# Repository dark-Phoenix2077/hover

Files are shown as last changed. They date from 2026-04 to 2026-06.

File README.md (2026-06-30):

# Hover
A fully custom mini racing/stunt drone with ML-assisted balancing, automatic stunts, and some level of autonomous operation without costly cameras or GPS.

Screenshot 2026-04-16 at 4 11 55 pm

## Why I built this

I wanted a challenge that forced me to learn PCB design and embedded firmware from 
scratch, but also let me apply the area I already know well - machine learning. Designing
a drone from a blank schematic, writing every driver by hand, and then training a custom 
tiny ML model felt like the right way to do all of that at once. My goal was simply to push my first ever hardware project as far as I could, not to have a completely polished project.

## What the project is

Hover is a tiny brushed micro quadcopter built entirely from custom hardware and
firmware. There is no off-the-shelf flight controller, no commercial RC receiver, and no
pre-written driver code. Everything was written/designed from scratch by me.

The system has two PCBs:

Flight Controller (FC): A 4-layer X-shaped PCB with a motor in each corner. It runs an
STM32F103C8T6 at 72MHz, an ICM-42688-P IMU over SPI, a BK2423 2.4GHz RF transceiver, 
and four brushed motor drive circuits.

Screenshot 2026-04-16 at 4 12 30 pm

Remote Control (RC): A 2-layer PCB inside a 3D-printed enclosure. It uses
the same STM32F103C8T6 and BK2423 RF ICs. It has two analog joysticks (ADC + DMA) for
throttle, yaw, pitch, and roll, and eight buttons which are used for arming, auto take-off, auto land,
return-to-home, a 360-degree flip trigger (one of my goals for this was to have some kind of smart one-button trick, and for this goal I settled on the 360 flip), and three spares for future use.

Screenshot 2026-04-16 at 4 14 29 pm

apart from that, this repository also includes:

ML Pipeline: A training and conversion pipeline for an onboard stabilisation model.
Training data will be collected from real flight telemetry once the hardware is
bought. The model will be converted to TFLite and dropped directly into the
FC firmware, which already has the inference code in place and waiting.

CAD: Both the drone body and RC enclosure were designed in Onshape. The drone frame
is a minimal 2-shell design with motor mounts, battery tray, and canopy, with both shells 
sandwiching the PCB in the middle. The RC enclosure uses the same 2-shell design with joystick 
cutouts, button extenders, and a battery bay below the PCB.

Screenshot 2026-04-16 at 4 15 18 pm

Screenshot 2026-04-16 at 4 16 22 pm

Firmware: Firmware created for both the FC and RC in STM32 CubeMX and CubeIDE, all firmware should work but is untested as I do not have the hardware right now. additionally, the ML inference file is writtenbut will not work until I create the .tflite model file.

BOM: A BOM generated from kicad for the FC & the RC and also other parts (excluding 3D printed parts and assorted screws). I will likely be purchasing all of these myself, and this is not completely final.

## Build Photos:





# Bill of Materials
FC

* Note that MPU-6050 is significantly cheaper locally, and that is why I chose to use it despite cheaper alternatives

| Reference | Component | Qty | Package | LCSC | Price/Unit |
|---|---|---|---|---|---|
| U2 | STM32F103C8T6 | 1 | LQFP-48 | https://www.lcsc.com/product-detail/C8734.html | $1.65 |
| U3 | MPU-6050 | 1 | QFN-24 | https://www.lcsc.com/product-detail/C24112.html | $6.88 |
| U4 | BK2423 | 1 | QFN-20 | https://www.lcsc.com/search?q=BK2423 | ~$0.80 |
| U1 | AMS1117-3.3 | 1 | SOT-223 | https://www.lcsc.com/product-detail/C347222.html | ~$0.10 |
| Y1, Y2 | 16MHz Crystal | 2 | SMD 3225-4Pin | https://www.lcsc.com/product-detail/C13738.html | $0.30 |
| Q1–Q4 | SI2300 MOSFET | 4 | SOT-23 | https://www.lcsc.com/product-detail/C6285728.html | $0.01 |
| D1–D4 | 1N4148 Flyback Diode | 4 | SOD-323 | https://www.lcsc.com/product-detail/C2972761.html | $0.006 |
| J1 | Battery Connector (1S) | 1 | JST-PH 2pin | https://www.lcsc.com/product-detail/C295747.html | ~$0.08 |
| J2–J5 | Motor Connector | 4 | JST-PH 2pin | https://www.lcsc.com/product-detail/C295747.html | ~$0.08 |
| J6 | SWD Header | 1 | 2.54mm 1×4 | https://www.lcsc.com/product-detail/C124375.html | ~$0.05 |
| J7 | Charge Port | 1 | Barrel Jack SMD | www.lcsc.com/product-detail/C16214.html | ~$0.20 |
| SW1 | Slide Switch | 1 | SMD SPDT | https://www.lcsc.com/product-detail/C431541.html | ~$0.12 |
| TP1–TP5 | Test Point 1.5mm | 5 | Pad D1.5mm | https://www.lcsc.com/search?q=testpoint+1.5mm | ~$0.02 |
| C1, C3, C19, C21 | 10µF Cap | 4 | 0805 | https://www.lcsc.com/search?q=0805+capacitor | ~$0.002 |
| C2, C4–C10, C14–C18, C20, C24 | 100nF Cap | 15 | 0402 | https://www.lcsc.com/search?q=0402+capacitor | ~$0.002 |
| C11 | 1µF Cap | 1 | 0402 | https://www.lcsc.com/search?q=0402+capacitor | ~$0.002 |
| C12, C13, C22, C23 | 22pF Cap | 4 | 0402 | https://www.lcsc.com/search?q=0402+capacitor | ~$0.002 |
| R1, R6, R8, R10, R12 | 10kΩ Resistor | 5 | 0402 | https://www.lcsc.com/search?q=0402+resistor | ~$0.002 |
| R2, R3 | 4.7kΩ Resistor | 2 | 0402 | https://www.lcsc.com/search?q=0402+resistor | ~$0.002 |
| R4 | 22kΩ Resistor | 1 | 0402 | https://www.lcsc.com/search?q=0402+resistor | ~$0.002 |
| R5, R7, R9, R11 | 100Ω Resistor | 4 | 0402 | https://www.lcsc.com/search?q=0402+resistor | ~$0.002 |

RC

| Reference | Component | Qty | Package | LCSC | Price/Unit |
|---|---|---|---|---|---|
| U4 | STM32F103C8T6 | 1 | LQFP-48 | https://www.lcsc.com/product-detail/C8734.html | $1.65 |
| U5 | BK2423 | 1 | QFN-20 | https://www.lcsc.com/search?q=BK2423 | ~$0.80 |
| U1 | AMS1117-3.3 | 1 | SOT-223 | https://www.lcsc.com/product-detail/C347222.html | ~$0.10 |
| Y2, Y3 | 16MHz Crystal | 2 | SMD 3225-4Pin | https://www.lcsc.com/product-detail/C13738.html | $0.30 |
| BZ1 | Buzzer | 1 | 12×9.5mm THT | — | — |
| D1 | LED Indicator | 1 | THT D1.8mm | — | — |
| J1 | Battery Connector (1S) | 1 | JST-PH 2pin | https://www.lcsc.com/product-detail/C295747.html | ~$0.08 |
| J2, J3 | Joystick Connector | 2 | 2.54mm 1×5 | — | — |
| J7 | SWD Header | 1 | 2.54mm 1×4 | https://www.lcsc.com/product-detail/C124375.html | ~$0.05 |
| J8 | Charge Port | 1 | Barrel Jack THT | https://www.lcsc.com/product-detail/C16214.html | ~$0.20 |
| SW1–SW8 | Push Button | 8 | THT 6mm | — | — |
| SW9 | Slide Switch | 1 | SMD SPDT | https://www.lcsc.com/product-detail/C431541.html | ~$0.12 |
| TP1 | Test Point 1.5mm (ANT) | 1 | Pad D1.5mm | https://www.lcsc.com/search?q=testpoint+1.5mm | ~$0.02 |
| C1, C3, C23, C31 | 10µF Cap | 4 | 0805 | https://www.lcsc.com/search?q=0805+capacitor | ~$0.002 |
| C2, C4, C14–C19, C24, C25, C28–C30 | 100nF Cap | 13 | 0402 | https://www.lcsc.com/search?q=0402+capacitor | ~$0.002 |
| C20 | 1µF Cap | 1 | 0402 | https://www.lcsc.com/search?q=0402+capacitor | ~$0.002 |
| C21, C22, C26, C27 | 22pF Cap | 4 | 0402 | https://www.lcsc.com/search?q=0402+capacitor | ~$0.002 |
| R1–R3 | 10kΩ Resistor | 3 | 0402 | https://www.lcsc.com/search?q=0402+resistor | ~$0.002 |
| R4 | 22kΩ Resistor | 1 | 0402 | https://www.lcsc.com/search?q=0402+resistor | ~$0.002 |
| R5, R6 | 100Ω Resistor | 2 | 0402 | https://www.lcsc.com/search?q=0402+resistor | ~$0.002 |

Other

* This list covers physical assembly components not part of either PCB
* It is not completely final - I made this off the top of my head, there are probably other components I forgot to identify
* It does not include miscellaneous screws or 3D printed parts

| Component | Qty | Notes | Price (est.) |
|---|---|---|---|
| Brushed coreless DC motors (8020) | 4 | 8×20mm form factor, 1S compatible | ~$2.00 each |
| 55mm micro quad propellers (CW) | 4 | Match motor shaft diameter | ~$0.50 each |
| 55mm micro quad propellers (CCW) | 4 | Match motor shaft diameter | ~$0.50 each |
| 1S LiPo battery — 150mAh (drone) | 1 | Fits battery tray in drone frame | ~$4.00 |
| 1S LiPo battery — 800mAh (RC) | 1 | Fits battery bay in RC enclosure | ~$6.00 |
| 31.25mm wire for 2.4GHz antenna (drone) | 1 | Bare solid-core wire, soldered to ANT test point on FC PCB; length = λ/4 at 2.4GHz | ~$0.10 |
| 31.25mm wire for 2.4GHz antenna (RC) | 1 | Same as above, for RC PCB ANT test point | ~$0.10 |
| Silicone motor wire (26AWG) | ~1m | Connects motors to PCB JST connectors | ~$1.00 |
| 1S LiPo charger (USB) | 1 | Compatible with JST-PH or barrel jack input | ~$5.00 |

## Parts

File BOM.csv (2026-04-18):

Board | Reference | Component | Qty | Package | LCSC Link | Price/Unit
FC | U2 | STM32F103C8T6 | 1 | LQFP-48 | https://www.lcsc.com/product-detail/C8734.html | $1.65
FC | U3 | MPU-6050 | 1 | QFN-24 | https://www.lcsc.com/product-detail/C24112.html | $6.88
FC | U4 | BK2423 | 1 | QFN-20 | https://www.lcsc.com/search?q=BK2423 | ~$0.80
FC | U1 | AMS1117-3.3 | 1 | SOT-223 | https://www.lcsc.com/product-detail/C347222.html | ~$0.10
FC | Y1, Y2 | 16MHz Crystal | 2 | SMD 3225-4Pin | https://www.lcsc.com/product-detail/C13738.html | $0.30
FC | Q1–Q4 | SI2300 MOSFET | 4 | SOT-23 | https://www.lcsc.com/product-detail/C6285728.html | $0.01
FC | D1–D4 | 1N4148 Flyback Diode | 4 | SOD-323 | https://www.lcsc.com/product-detail/C2972761.html | $0.006
FC | J1 | Battery Connector (1S) | 1 | JST-PH 2pin | https://www.lcsc.com/product-detail/C295747.html | ~$0.08
FC | J2–J5 | Motor Connector | 4 | JST-PH 2pin | https://www.lcsc.com/product-detail/C295747.html | ~$0.08
FC | J6 | SWD Header | 1 | 2.54mm 1×4 | https://www.lcsc.com/product-detail/C124375.html | ~$0.05
FC | J7 | Charge Port | 1 | Barrel Jack SMD | https://www.lcsc.com/product-detail/C16214.html | ~$0.20
FC | SW1 | Slide Switch | 1 | SMD SPDT | https://www.lcsc.com/product-detail/C431541.html | ~$0.12
FC | TP1–TP5 | Test Point 1.5mm | 5 | Pad D1.5mm | https://www.lcsc.com/search?q=testpoint+1.5mm | ~$0.02
FC | C1, C3, C19, C21 | 10µF Cap | 4 | 0805 | https://www.lcsc.com/search?q=0805+capacitor | ~$0.002
FC | C2, C4–C10, C14–C18, C20, C24 | 100nF Cap | 15 | 0402 | https://www.lcsc.com/search?q=0402+capacitor | ~$0.002
FC | C11 | 1µF Cap | 1 | 0402 | https://www.lcsc.com/search?q=0402+capacitor | ~$0.002
FC | C12, C13, C22, C23 | 22pF Cap | 4 | 0402 | https://www.lcsc.com/search?q=0402+capacitor | ~$0.002
FC | R1, R6, R8, R10, R12 | 10kΩ Resistor | 5 | 0402 | https://www.lcsc.com/search?q=0402+resistor | ~$0.002
FC | R2, R3 | 4.7kΩ Resistor | 2 | 0402 | https://www.lcsc.com/search?q=0402+resistor | ~$0.002
FC | R4 | 22kΩ Resistor | 1 | 0402 | https://www.lcsc.com/search?q=0402+resistor | ~$0.002
FC | R5, R7, R9, R11 | 100Ω Resistor | 4 | 0402 | https://www.lcsc.com/search?q=0402+resistor | ~$0.002
RC | U4 | STM32F103C8T6 | 1 | LQFP-48 | https://www.lcsc.com/product-detail/C8734.html | $1.65
RC | U5 | BK2423 | 1 | QFN-20 | https://www.lcsc.com/search?q=BK2423 | ~$0.80
RC | U1 | AMS1117-3.3 | 1 | SOT-223 | https://www.lcsc.com/product-detail/C347222.html | ~$0.10
RC | Y2, Y3 | 16MHz Crystal | 2 | SMD 3225-4Pin | https://www.lcsc.com/product-detail/C13738.html | $0.30
RC | BZ1 | Buzzer | 1 | 12×9.5mm THT | https://www.lcsc.com/product-detail/C96093.html | ~$0.50
RC | D1 | LED Indicator | 1 | THT D1.8mm | https://www.lcsc.com/search?q=LED+1.8mm+THT | ~$0.05
RC | J1 | Battery Connector (1S) | 1 | JST-PH 2pin | https://www.lcsc.com/product-detail/C295747.html | ~$0.08
RC | J2, J3 | Joystick Connector | 2 | 2.54mm 1×5 | https://www.lcsc.com/search?q=2.54mm+1x5+header | ~$0.05
RC | J7 | SWD Header | 1 | 2.54mm 1×4 | https://www.lcsc.com/product-detail/C124375.html | ~$0.05
RC | J8 | Charge Port | 1 | Barrel Jack THT | https://www.lcsc.com/product-detail/C16214.html | ~$0.20
RC | SW1–SW8 | Push Button | 8 | THT 6mm | https://www.lcsc.com/product-detail/C285474.html | ~$0.10
RC | SW9 | Slide Switch | 1 | SMD SPDT | https://www.lcsc.com/product-detail/C431541.html | ~$0.12
RC | TP1 | Test Point 1.5mm (ANT) | 1 | Pad D1.5mm | https://www.lcsc.com/search?q=testpoint+1.5mm | ~$0.02
RC | C1, C3, C23, C31 | 10µF Cap | 4 | 0805 | https://www.lcsc.com/search?q=0805+capacitor | ~$0.002
RC | C2, C4, C14–C19, C24, C25, C28–C30 | 100nF Cap | 13 | 0402 | https://www.lcsc.com/search?q=0402+capacitor | ~$0.002
RC | C20 | 1µF Cap | 1 | 0402 | https://www.lcsc.com/search?q=0402+capacitor | ~$0.002
RC | C21, C22, C26, C27 | 22pF Cap | 4 | 0402 | https://www.lcsc.com/search?q=0402+capacitor | ~$0.002
RC | R1–R3 | 10kΩ Resistor | 3 | 0402 | https://www.lcsc.com/search?q=0402+resistor | ~$0.002
RC | R4 | 22kΩ Resistor | 1 | 0402 | https://www.lcsc.com/search?q=0402+resistor | ~$0.002
RC | R5, R6 | 100Ω Resistor | 2 | 0402 | https://www.lcsc.com/search?q=0402+resistor | ~$0.002
Other | — | Brushed coreless DC motors (8020) | 4 | 8×20mm | https://www.lcsc.com/search?q=8020+coreless+motor | ~$2.00
Other | — | 55mm micro quad propellers (CW) | 4 | 55mm | https://www.lcsc.com/search?q=55mm+propeller+CW | ~$0.50
Other | — | 55mm micro quad propellers (CCW) | 4 | 55mm | https://www.lcsc.com/search?q=55mm+propeller+CCW | ~$0.50
Other | — | 1S LiPo battery — 150mAh (drone) | 1 | — | https://www.lcsc.com/search?q=1S+150mAh+lipo | ~$4.00
Other | — | 1S LiPo battery — 800mAh (RC) | 1 | — | https://www.lcsc.com/search?q=1S+800mAh+lipo | ~$6.00
Other | — | 31.25mm wire for 2.4GHz antenna (drone) | 1 | — | https://www.lcsc.com/search?q=solid+core+wire | ~$0.10
Other | — | 31.25mm wire for 2.4GHz antenna (RC) | 1 | — | https://www.lcsc.com/search?q=solid+core+wire | ~$0.10
Other | — | Silicone motor wire (26AWG) | 1 | ~1m | https://www.lcsc.com/search?q=26AWG+silicone+wire | ~$1.00
Other | — | 1S LiPo charger (USB) | 1 | — | https://www.lcsc.com/search?q=1S+lipo+USB+charger | ~$5.00

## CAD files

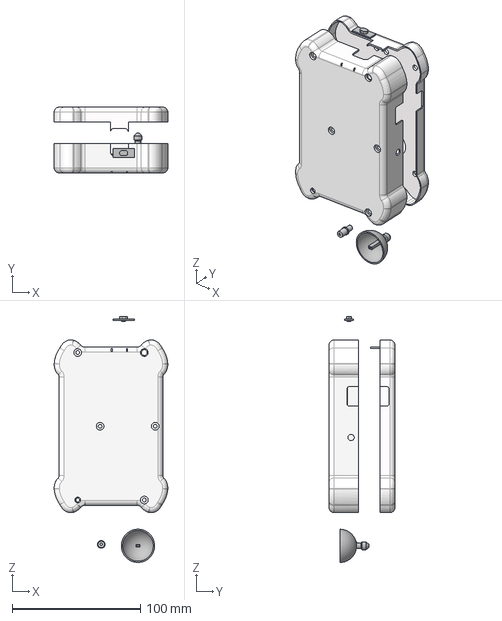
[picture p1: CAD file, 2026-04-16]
CAD/RC Case.step
88.7 x 51.4 x 191.9 mm

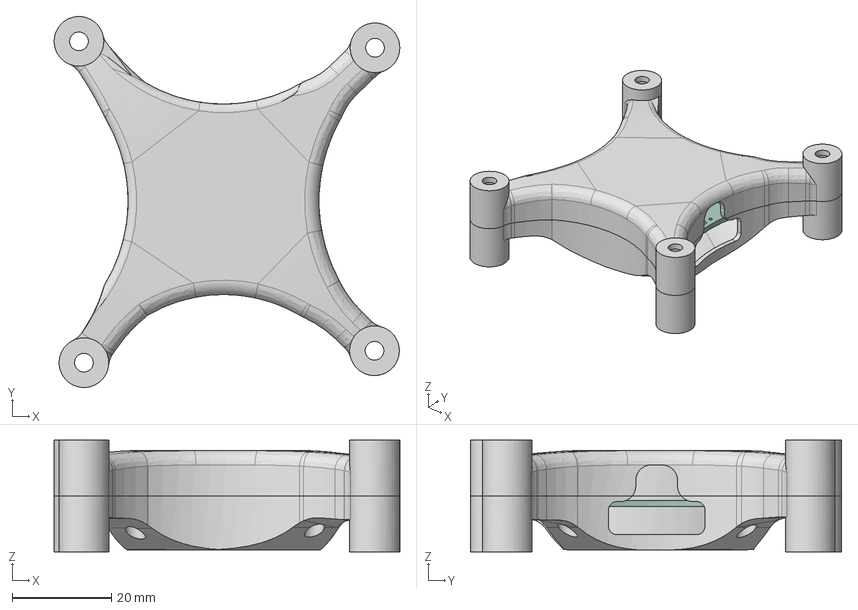
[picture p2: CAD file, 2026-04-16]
CAD/Drone Case.step
69.6 x 74.7 x 22.5 mm

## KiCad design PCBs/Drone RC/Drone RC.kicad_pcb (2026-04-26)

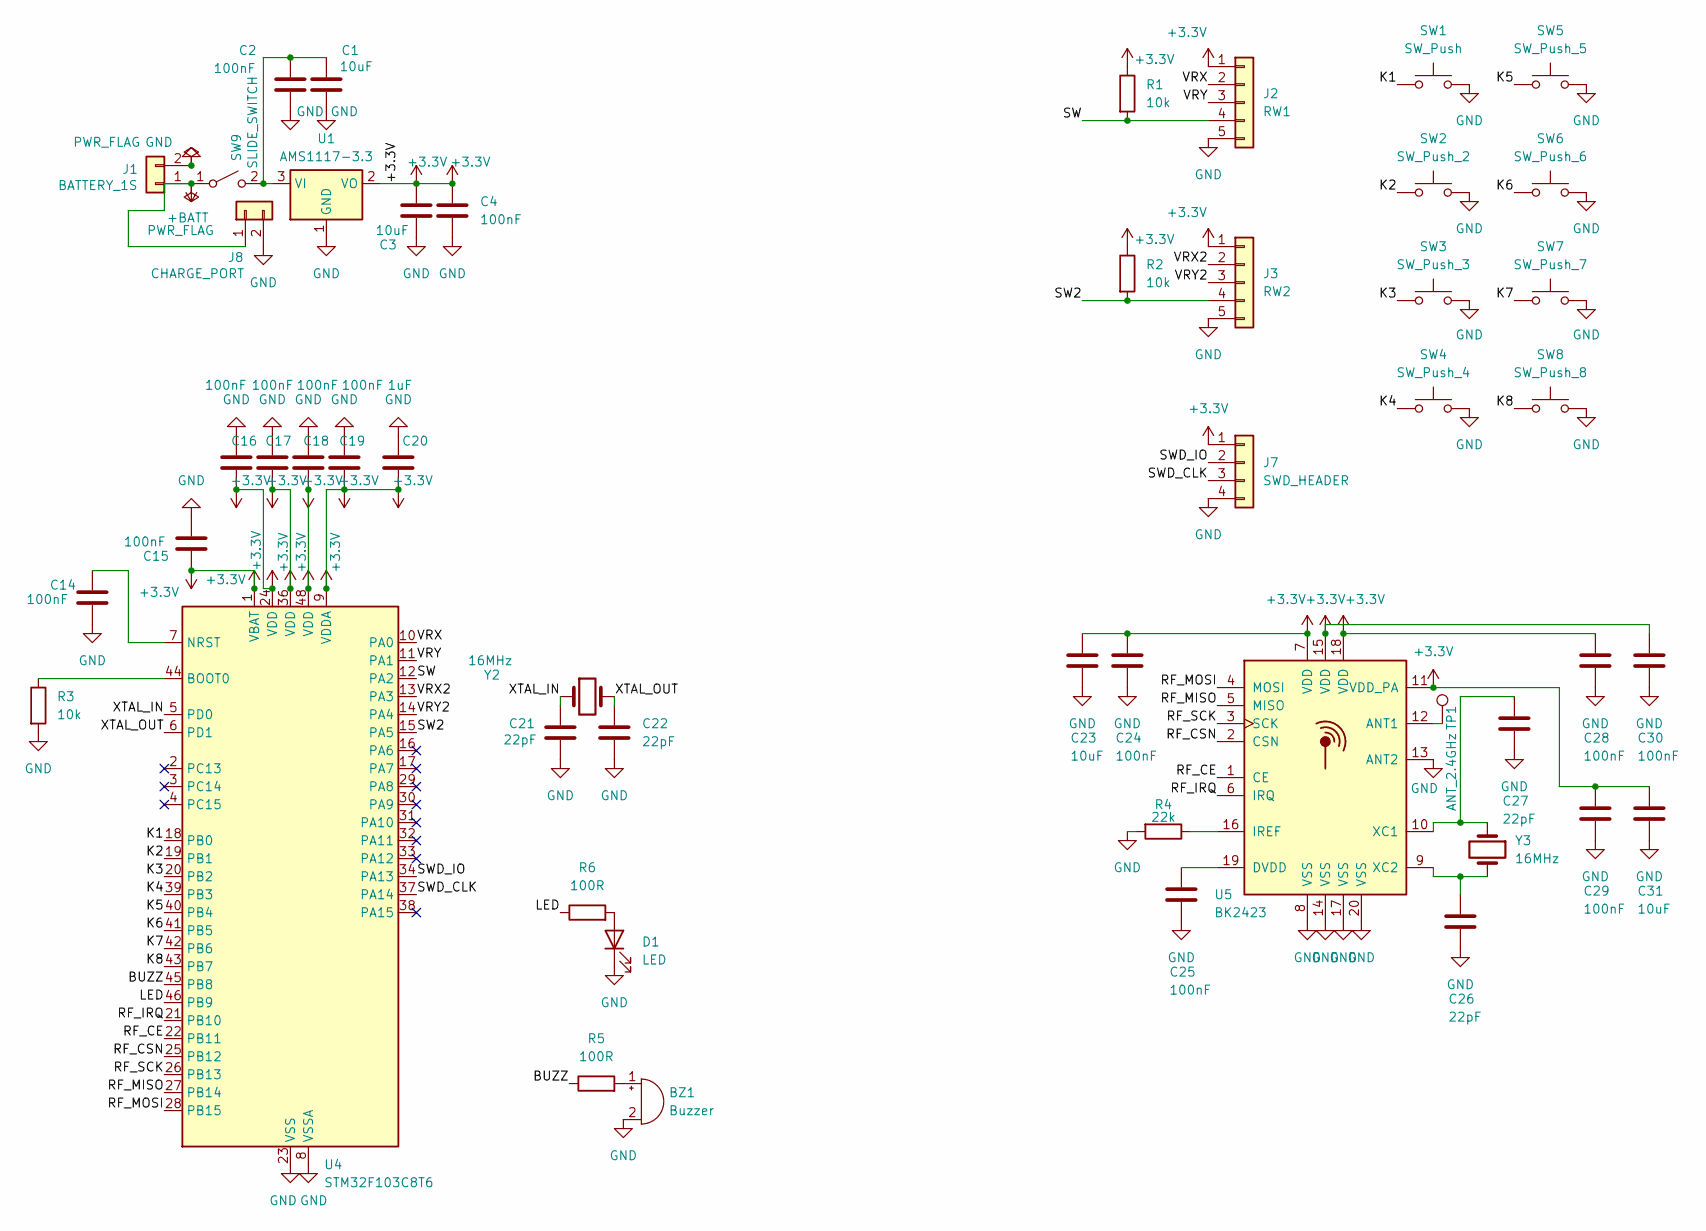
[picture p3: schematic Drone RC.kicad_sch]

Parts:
BZ1: Buzzer; Buzzer_12x9.5RM7.6
C1, C3, C23, C31: 10uF; C_0805_2012Metric
C2, C4, C14, C15, C16, C17, C18, C19, C24, C25, C28, C29, C30: 100nF; C_0402_1005Metric
C20: 1uF; C_0402_1005Metric
C21, C22, C26, C27: 22pF; C_0402_1005Metric
D1: LED; LED_D1.8mm_W1.8mm_H2.4mm_Horizontal_O1.27mm_Z1.6mm
J1: BATTERY_1S; JST_PH_B2B-PH-K_1x02_P2.00mm_Vertical
J2: RW1; PinHeader_1x05_P2.54mm_Vertical
J3: RW2; PinHeader_1x05_P2.54mm_Vertical
J7: SWD_HEADER; PinHeader_1x04_P2.54mm_Vertical
J8: CHARGE_PORT; BarrelJack_CUI_PJ-102AH_Horizontal
R1, R2, R3: 10k; R_0402_1005Metric
R4: 22k; R_0402_1005Metric
R5, R6: 100R; R_0402_1005Metric
SW1: SW_Push; SW_PUSH_6mm
SW2: SW_Push_2; SW_PUSH_6mm
SW3: SW_Push_3; SW_PUSH_6mm
SW4: SW_Push_4; SW_PUSH_6mm
SW5: SW_Push_5; SW_PUSH_6mm
SW6: SW_Push_6; SW_PUSH_6mm
SW7: SW_Push_7; SW_PUSH_6mm
SW8: SW_Push_8; SW_PUSH_6mm
SW9: SLIDE_SWITCH; SW_SPDT_CK_JS102011SAQN
TP1: ANT_2.4GHz; TestPoint_Pad_D1.5mm
U1: AMS1117-3.3; SOT-223-3_TabPin2
U4: STM32F103C8T6; LQFP-48_7x7mm_P0.5mm
U5: BK2423; QFN-20-1EP_4x4mm_P0.5mm_EP2.5x2.5mm
Y2, Y3: 16MHz; Crystal_SMD_3225-4Pin_3.2x2.5mm

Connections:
+3.3V: C3.1, C4.1, C15.1, C16.1, C17.1, C18.1, C19.1, C20.1, C23.1, C24.1, C28.1, C29.1, C30.1, C31.1, J2.1, J3.1, J7.1, R1.1, R2.1, U1.2 (VO), U4.1 (VBAT), U4.9 (VDDA), U4.24 (VDD), U4.36 (VDD), U4.48 (VDD), U5.7 (VDD), U5.11 (VDD_PA), U5.15 (VDD), U5.18 (VDD)
+BATT: J1.1, J8.1, SW9.1 (A)
/BUZZ: R5.1, U4.45 (PB8)
/K1: SW1.1, U4.18 (PB0)
/K2: SW2.1, U4.19 (PB1)
/K3: SW3.1, U4.20 (PB2)
/K4: SW4.1, U4.39 (PB3)
/K5: SW5.1, U4.40 (PB4)
/K6: SW6.1, U4.41 (PB5)
/K7: SW7.1, U4.42 (PB6)
/K8: SW8.1, U4.43 (PB7)
/LED: R6.1, U4.46 (PB9)
/RF_CE: U4.22 (PB11), U5.1 (CE)
/RF_CSN: U4.25 (PB12), U5.2 (CSN)
/RF_IRQ: U4.21 (PB10), U5.6 (IRQ)
/RF_MISO: U4.27 (PB14), U5.5 (MISO)
/RF_MOSI: U4.28 (PB15), U5.4 (MOSI)
/RF_SCK: U4.26 (PB13), U5.3 (SCK)
/SW: J2.4, R1.2, U4.12 (PA2)
/SW2: J3.4, R2.2, U4.15 (PA5)
/SWD_CLK: J7.3, U4.37 (PA14)
/SWD_IO: J7.2, U4.34 (PA13)
/VRX: J2.2, U4.10 (PA0)
/VRX2: J3.2, U4.13 (PA3)
/VRY: J2.3, U4.11 (PA1)
/VRY2: J3.3, U4.14 (PA4)
/XTAL_IN: C21.1, U4.5 (PD0), Y2.1
/XTAL_OUT: C22.1, U4.6 (PD1), Y2.2
GND: BZ1.2 (-), C1.2, C2.2, C3.2, C4.2, C14.2, C15.2, C16.2, C17.2, C18.2, C19.2, C20.2, C21.2, C22.2, C23.2, C24.2, C25.2, C26.2, C27.2, C28.2, C29.2, C30.2, C31.2, D1.1 (K), J1.2, J2.5, J3.5, J7.4, J8.2, R3.2, R4.2, SW1.2, SW2.2, SW3.2, SW4.2, SW5.2, SW6.2, SW7.2, SW8.2, U1.1 (GND), U4.8 (VSSA), U4.23 (VSS), U4.35 (VSS), U4.47 (VSS), U5.8 (VSS), U5.13 (ANT2), U5.14 (VSS), U5.17 (VSS), U5.20 (VSS)
unnamed: BZ1.1 (+), R5.2
unnamed: D1.2 (A), R6.2
unnamed: C1.1, C2.1, SW9.2 (B), U1.3 (VI)
unnamed: R3.1, U4.44 (BOOT0)
unnamed: C14.1, U4.7 (NRST)
unnamed: TP1.1 (1_1), U5.12 (ANT1)
unnamed: C25.1, U5.19 (DVDD)
unnamed: R4.1, U5.16 (IREF)
unnamed: C27.1, U5.10 (XC1), Y3.1
unnamed: C26.1, U5.9 (XC2), Y3.2

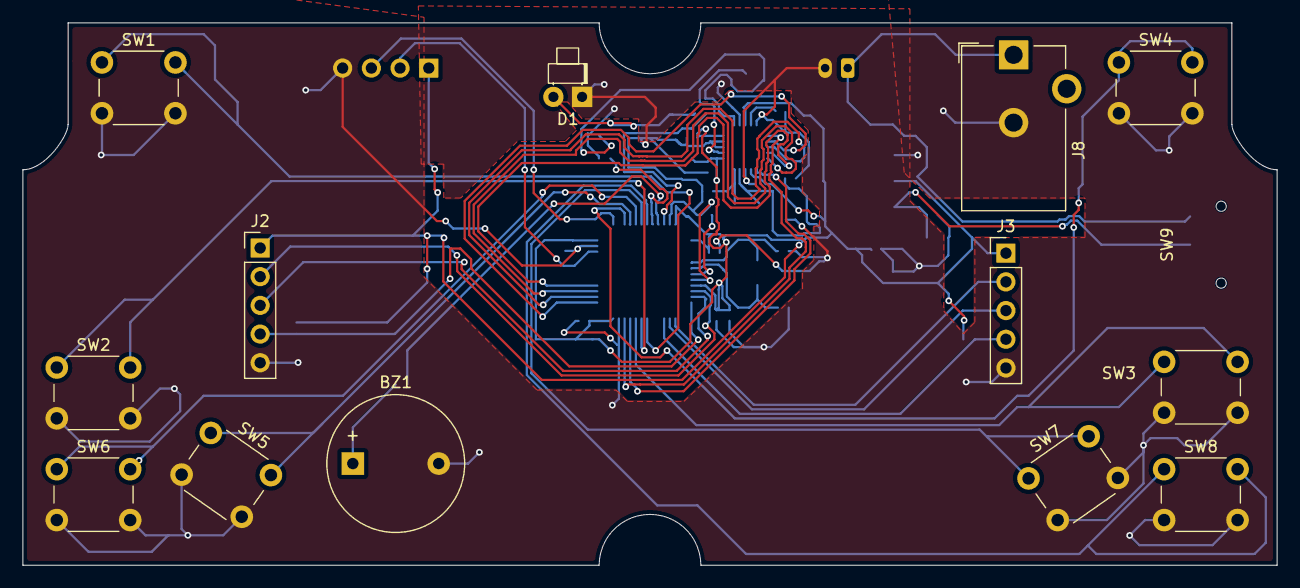
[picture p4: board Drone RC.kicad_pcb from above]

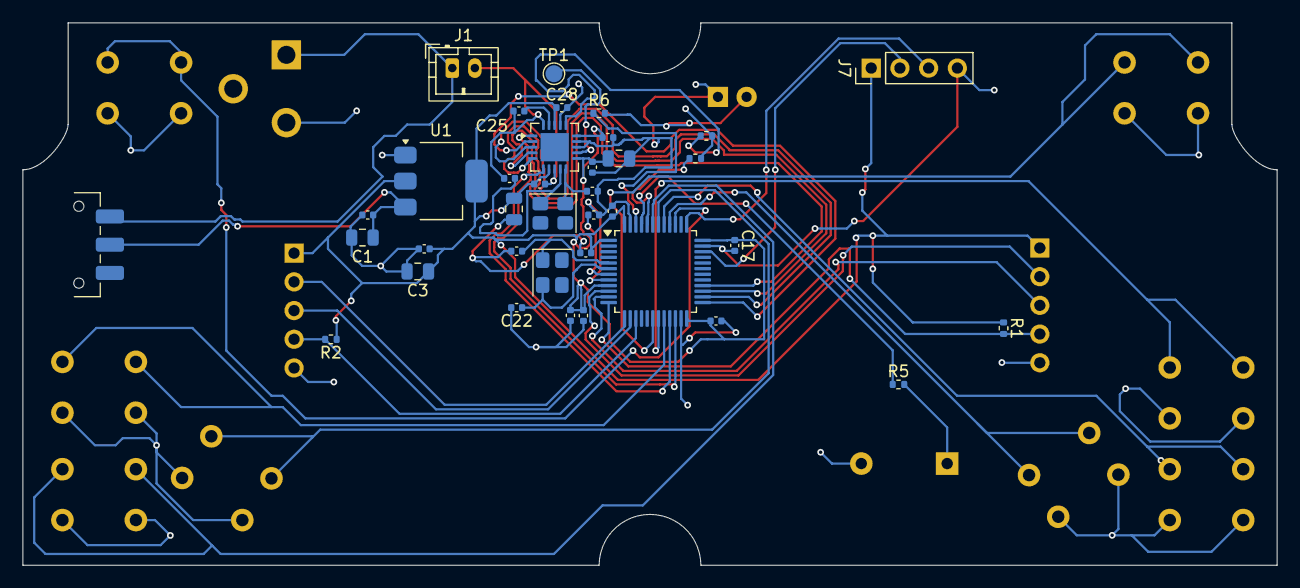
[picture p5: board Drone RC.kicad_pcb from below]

Board: 2 copper layers, 111.0 x 48.0 mm, 50 parts (37 on the bottom side), 39 nets.

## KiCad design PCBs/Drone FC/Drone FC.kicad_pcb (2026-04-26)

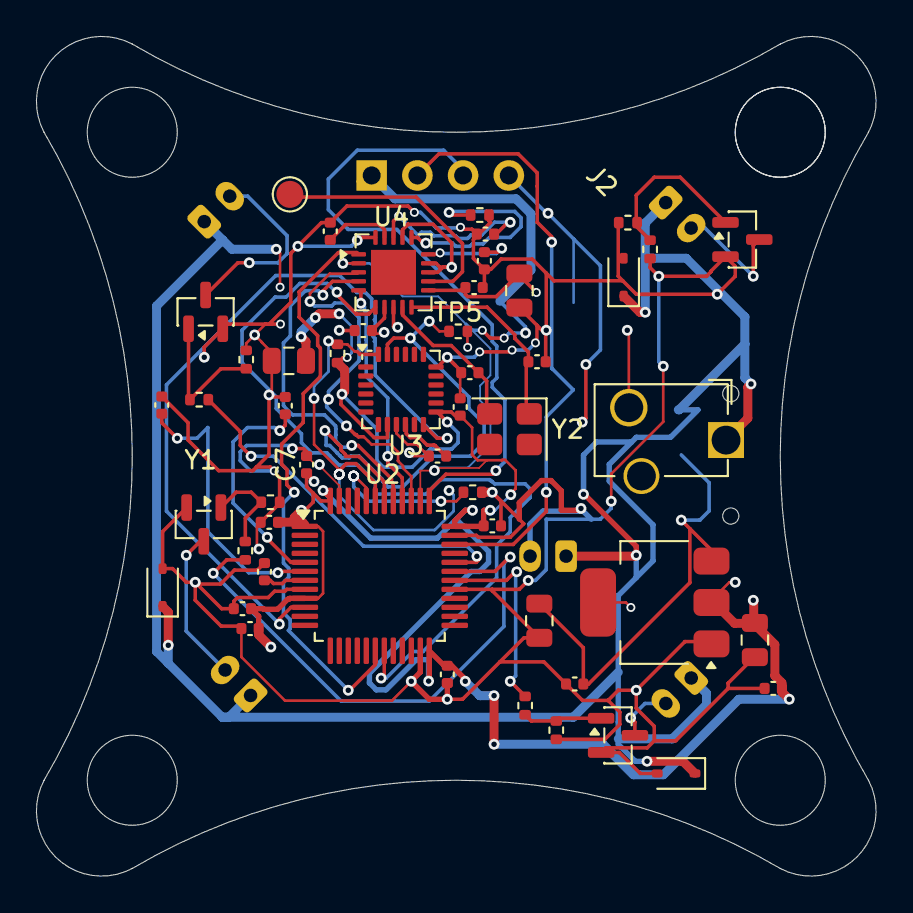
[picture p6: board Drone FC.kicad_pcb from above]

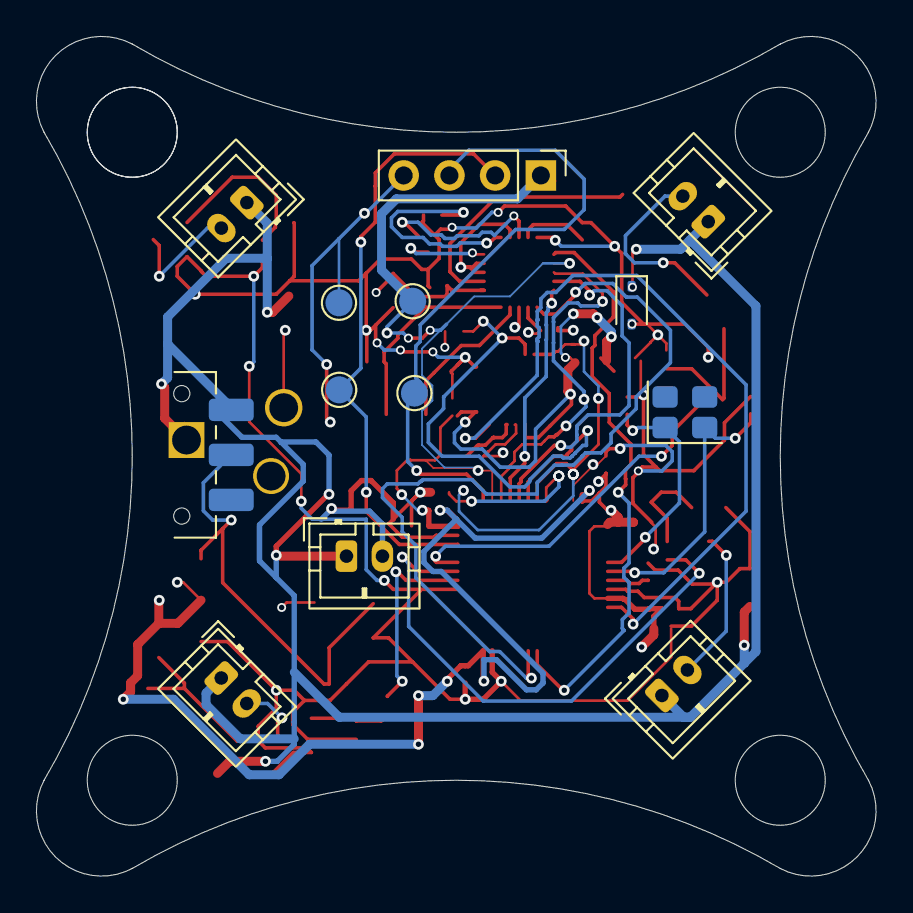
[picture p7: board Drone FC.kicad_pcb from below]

Board: 4 copper layers, 46.6 x 46.6 mm, 63 parts (13 on the bottom side), 37 nets.

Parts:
C1, C3, C19, C21: 10uF; C_0805_2012Metric
C2, C4, C5, C6, C7, C8, C9, C10, C14, C15, C16, C17, C18, C20, C24: 100nF; C_0402_1005Metric
C11: 1uF; C_0402_1005Metric
C12, C13, C22, C23: 22pF; C_0402_1005Metric
D1, D2, D3, D4: 1N4148; D_SOD-323
J1: BATTERY_1S; JST_PH_B2B-PH-K_1x02_P2.00mm_Vertical
J2: MOTOR1; JST_PH_B2B-PH-K_1x02_P2.00mm_Vertical
J3: MOTOR2; JST_PH_B2B-PH-K_1x02_P2.00mm_Vertical
J4: MOTOR3; JST_PH_B2B-PH-K_1x02_P2.00mm_Vertical
J5: MOTOR4; JST_PH_B2B-PH-K_1x02_P2.00mm_Vertical
J6: SWD_HEADER; PinHeader_1x04_P2.54mm_Vertical
J7: CHARGE_PORT; DC-011D_SMD_Horizontal
Q1, Q2, Q3, Q4: SI2300; SOT-23
R1, R6, R8, R10, R12: 10k; R_0402_1005Metric
R2, R3: 4.7k; R_0402_1005Metric
R4: 22k; R_0402_1005Metric
R5, R7, R9, R11: 100R; R_0402_1005Metric
SW1: SLIDE_SWITCH; SW_SPDT_CK_JS102011SAQN
TP1: ANT_2.4GHz; TestPoint_Pad_D1.5mm
TP2: D; TestPoint_Pad_D1.5mm
TP3: C; TestPoint_Pad_D1.5mm
TP4: GND; TestPoint_Pad_D1.5mm
TP5: VCC; TestPoint_Pad_D1.5mm
U1: AMS1117-3.3; SOT-223-3_TabPin2
U2: STM32F103C8T6; LQFP-48_7x7mm_P0.5mm
U3: MPU-6050; InvenSense_QFN-24_4x4mm_P0.5mm
U4: BK2423; QFN-20-1EP_4x4mm_P0.5mm_EP2.5x2.5mm
Y1, Y2: 16MHz; Crystal_SMD_3225-4Pin_3.2x2.5mm

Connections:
+3.3V: C16.1, C17.1, C18.1, C20.1, C21.1, R3.1, U1.2 (VO), U4.7 (VDD), U4.11 (VDD_PA), U4.15 (VDD), U4.18 (VDD)
+BATT: D1.1 (K), D2.1 (K), D3.1 (K), D4.1 (K), J1.1, J2.1, J3.1, J4.1, J5.1, J7.1, SW1.1 (A)
/IMU_INT: U2.10 (PA0), U3.12 (INT)
/IMU_SCL: R3.2, U2.42 (PB6), U3.23 (SCL)
/IMU_SDA: R2.2, U2.43 (PB7), U3.24 (SDA)
/MOTOR1_PWM: C1.2, C2.2, C3.2, C4.2, C5.2, C6.2, C7.2, C8.2, C9.2, C10.2, C11.2, C12.2, C13.2, C14.2, C16.2, C17.2, C19.2, C20.2, C21.2, C22.2, C23.2, C24.2, D1.2 (A), D2.2 (A), D3.2 (A), D4.2 (A), J1.2, Q1.2 (S), Q2.2 (S), Q3.2 (S), Q4.2 (S), R1.2, R4.2, R5.2, R6.2, R8.2, R10.2, R12.2, U1.1 (GND), U2.8 (VSSA), U2.23 (VSS), U2.29 (PA8), U2.35 (VSS), U2.47 (VSS), U3.18 (GND), U4.20 (VSS)
/MOTOR2_PWM: R7.2, U2.30 (PA9)
/MOTOR3_PWM: R9.2, U2.31 (PA10)
/MOTOR4_PWM: R11.2, U2.32 (PA11)
/RF_CE: U2.18 (PB0), U4.1 (CE)
/RF_CSN: C3.1, C4.1, C5.1, C6.1, C7.1, C8.1, C10.1, C11.1, C14.1, C19.1, J6.1, R2.1, TP5.1 (1_1), U1.2 (VO), U2.1 (VBAT), U2.9 (VDDA), U2.24 (VDD), U2.36 (VDD), U2.38 (PA15), U2.48 (VDD), U3.8 (VLOGIC), U3.13 (VDD), U4.2 (CSN)
/RF_IRQ: U2.19 (PB1), U4.6 (IRQ)
/RF_MISO: U2.40 (PB4), U4.5 (MISO)
/RF_MOSI: U2.41 (PB5), U4.4 (MOSI)
/RF_SCK: U2.39 (PB3), U4.3 (SCK)
/SWD_CLK: J6.3, TP3.1 (1_1), U2.37 (PA14)
/SWD_IO: J6.2, TP2.1 (1_1), U2.34 (PA13)
/XTAL_IN: C12.1, U2.5 (PD0), Y1.1
/XTAL_OUT: C13.1, U2.6 (PD1), Y1.2
GND: C15.2, C18.2, J6.4, J7.2, TP4.1 (1_1), U3.9 (AD0), U4.8 (VSS), U4.13 (ANT2), U4.14 (VSS), U4.17 (VSS)
unnamed: J2.2, Q1.3 (D)
unnamed: J3.2, Q2.3 (D)
unnamed: J4.2, Q3.3 (D)
unnamed: J5.2, Q4.3 (D)
unnamed: Q1.1 (G), R5.1, R6.1
unnamed: Q2.1 (G), R7.1, R8.1
unnamed: Q3.1 (G), R9.1, R10.1
unnamed: Q4.1 (G), R11.1, R12.1
unnamed: C1.1, C2.1, SW1.2 (B), U1.3 (VI)
unnamed: R1.1, U2.44 (BOOT0)
unnamed: C9.1, U2.7 (NRST)
unnamed: C15.1, U3.10 (REGOUT)
unnamed: TP1.1 (1_1), U4.12 (ANT1)
unnamed: C24.1, U4.19 (DVDD)
unnamed: R4.1, U4.16 (IREF)
unnamed: C22.1, U4.10 (XC1), Y2.1
unnamed: C23.1, U4.9 (XC2), Y2.2

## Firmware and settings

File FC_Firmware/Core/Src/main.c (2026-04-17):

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
/* Includes ------------------------------------------------------------------*/
#include "main.h"

SPI_HandleTypeDef hspi1;
SPI_HandleTypeDef hspi2;

TIM_HandleTypeDef htim1;

UART_HandleTypeDef huart2;

/* USER CODE BEGIN PV */
static ICM_Handle  icm = { &hspi2, IMU_CS_GPIO_Port, IMU_CS_Pin };
static NRF_Handle  nrf = { &hspi1, RF_CE_GPIO_Port,  RF_CE_Pin,
                                    RF_CSN_GPIO_Port, RF_CSN_Pin };
static ICM_Data    imu_data;
static ICM_Offsets imu_off;
static RC_Packet   pkt;
static bool        pkt_fresh = false;
/* USER CODE END PV */

void SystemClock_Config(void);
static void MX_GPIO_Init(void);
static void MX_SPI1_Init(void);
static void MX_SPI2_Init(void);
static void MX_TIM1_Init(void);
static void MX_USART2_UART_Init(void);
/**
  * @brief  The application entry point.
  * @retval int
  */
int main(void)
{

  /* MCU Configuration--------------------------------------------------------*/

  /* Reset of all peripherals, Initializes the Flash interface and the Systick. */
  HAL_Init();

  /* Configure the system clock */
  SystemClock_Config();

  /* Initialize all configured peripherals */
  MX_GPIO_Init();
  MX_SPI1_Init();
  MX_SPI2_Init();
  MX_TIM1_Init();
  MX_USART2_UART_Init();

  /* USER CODE BEGIN 2 */
  SF_Init();
  if (ICM_Init(&icm) != HAL_OK) { Error_Handler(); }
  ICM_Calibrate(&icm, &imu_off);
  NRF_Init_RX(&nrf);
  Motor_Init(&htim1);
  FC_Init();
  /* USER CODE END 2 */

  /* Infinite loop */
  /* USER CODE BEGIN WHILE */
  while (1) {
      if (HAL_GPIO_ReadPin(IMU_INT_GPIO_Port, IMU_INT_Pin) == GPIO_PIN_SET) {
          ICM_Read(&icm, &imu_data);
          pkt_fresh = NRF_Receive(&nrf, &pkt);
          FC_Update(pkt_fresh ? &pkt : NULL, &imu_data, &imu_off);
      }
  /* USER CODE END WHILE */
  }

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


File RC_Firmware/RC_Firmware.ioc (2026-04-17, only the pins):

Mcu.UserName=STM32F103C8Tx
PA0-WKUP.Signal=ADCx_IN0
PA1.Signal=ADCx_IN1
PA10.Signal=USART1_RX
PA11.GPIO_Label=BTN_ARM
PA11.Signal=GPIO_Input
PA12.GPIO_Label=BTN_FLIP
PA12.Signal=GPIO_Input
PA13.Signal=SYS_JTMS-SWDIO
PA14.Signal=SYS_JTCK-SWCLK
PA2.Signal=ADCx_IN2
PA3.Signal=ADCx_IN3
PA4.Signal=ADCx_IN4
PA5.Signal=SPI1_SCK
PA6.Signal=SPI1_MISO
PA7.Signal=SPI1_MOSI
PA8.GPIO_Label=RF_CE
PA8.Signal=GPIO_Output
PA9.Signal=USART1_TX
PB0.GPIO_Label=RF_CSN
PB0.Signal=GPIO_Output
PB1.GPIO_Label=RF_IRQ
PB1.Signal=GPIO_Input
PB3.GPIO_Label=BTN_SP1
PB3.Signal=GPIO_Input
PB4.GPIO_Label=BTN_SP2
PB4.Signal=GPIO_Input
PB5.GPIO_Label=BTN_SP3
PB5.Signal=GPIO_Input
PB6.GPIO_Label=BTN_LAND
PB6.Signal=GPIO_Input
PB7.GPIO_Label=BTN_TKOFF
PB7.Signal=GPIO_Input
PB8.GPIO_Label=BTN_RTH
PB8.Signal=GPIO_Input
PB9.GPIO_Label=BUZZ
PB9.Signal=GPIO_Output
PD0-OSC_IN.Signal=RCC_OSC_IN
PD1-OSC_OUT.Signal=RCC_OSC_OUT

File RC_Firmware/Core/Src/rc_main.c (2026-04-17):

#include "main.h"
#include "bk2423.h"
#include <string.h>

extern SPI_HandleTypeDef hspi1;
extern ADC_HandleTypeDef hadc;

static NRF_Handle nrf = {
    &hspi1,
    RF_CE_GPIO_Port,  RF_CE_Pin,
    RF_CSN_GPIO_Port, RF_CSN_Pin
};

static uint16_t adc_buf[5];

typedef struct { GPIO_TypeDef *port; uint16_t pin; } BtnDef;
static const BtnDef BTNS[8] = {
    {BTN_ARM_GPIO_Port,       BTN_ARM_Pin      },
    {BTN_FLIP_GPIO_Port,      BTN_FLIP_Pin     },
    {BTN_LAND_GPIO_Port,      BTN_LAND_Pin     },
    {BTN_TKOFF_GPIO_Port,     BTN_TKOFF_Pin    },
    {BTN_RTH_GPIO_Port,       BTN_RTH_Pin      },
    {BTN_SP1_GPIO_Port,       BTN_SP1_Pin      },
    {BTN_SP2_GPIO_Port,       BTN_SP2_Pin      },
    {BTN_SP3_GPIO_Port,       BTN_SP3_Pin      },
};

static uint8_t  btn_state[8], btn_prev[8];
static uint32_t btn_timer[8];
#define DEBOUNCE_MS 20
#define BATT_LOW_THRESH 620

static void debounce_buttons(void){
    uint32_t now=HAL_GetTick();
    for(int i=0;i<8;i++){
        uint8_t raw=(HAL_GPIO_ReadPin(BTNS[i].port,BTNS[i].pin)==GPIO_PIN_RESET)?1:0;
        if(raw!=btn_prev[i]){ btn_timer[i]=now; btn_prev[i]=raw; }
        if(now-btn_timer[i]>=DEBOUNCE_MS) btn_state[i]=raw;
    }
}

static int16_t stick(uint16_t raw, bool inv){
    int32_t v=((int32_t)raw-2047)*500/2047;
    v=(v>500)?500:(v<-500)?-500:v;
    return inv?(int16_t)(-v):(int16_t)v;
}
static uint16_t throttle(uint16_t raw){
    uint32_t t=(uint32_t)raw*1000/4095;
    return (uint16_t)(t>1000?1000:t);
}

void rc_main(void){
    NRF_Init_TX(&nrf);
    HAL_ADC_Start_DMA(&hadc,(uint32_t*)adc_buf,5);
    memset(btn_state,0,sizeof(btn_state));
    memset(btn_prev, 0,sizeof(btn_prev));
    memset(btn_timer,0,sizeof(btn_timer));

    bool armed=false, prev_arm=false;
    uint32_t last_tx=0, last_beep=0;
    HAL_GPIO_WritePin(LED_GPIO_Port,LED_Pin,GPIO_PIN_SET);

    while(1){
        debounce_buttons();

        if(btn_state[0] && !prev_arm) armed=!armed;
        prev_arm=btn_state[0];

        if(adc_buf[4]<BATT_LOW_THRESH){
            uint32_t now=HAL_GetTick();
            if(now-last_beep>2000){
                HAL_GPIO_WritePin(BUZZER_GPIO_Port,BUZZER_Pin,GPIO_PIN_SET);
                HAL_Delay(80);
                HAL_GPIO_WritePin(BUZZER_GPIO_Port,BUZZER_Pin,GPIO_PIN_RESET);
                last_beep=now;
            }
        }

        /* 100 Hz TX loop */
        if(HAL_GetTick()-last_tx>=10){
            last_tx=HAL_GetTick();
            RC_Packet pkt;
            pkt.throttle = throttle(adc_buf[0]);
            pkt.yaw      = stick(adc_buf[1],false);
            pkt.pitch    = stick(adc_buf[2],true);
            pkt.roll     = stick(adc_buf[3],false);
            pkt.flags    = 0;
            if(armed)         pkt.flags|=0x01;
            if(btn_state[1])  pkt.flags|=0x02;
            if(btn_state[2])  pkt.flags|=0x04;
            NRF_Transmit(&nrf,&pkt);
            HAL_GPIO_TogglePin(LED_GPIO_Port,LED_Pin);
        }
    }
}

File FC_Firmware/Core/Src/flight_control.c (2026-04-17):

#include "flight_control.h"
#include <math.h>
#include <string.h>

#define RP_KP 0.6f
#define RP_KI 0.01f
#define RP_KD 0.02f
#define YR_KP 1.2f
#define YR_KI 0.005f
#define ANG_KP 4.0f

static PID pid_rr, pid_pr, pid_yr;
static PID pid_ra, pid_pa;
static FC_State state = FC_DISARMED;
static Attitude att;
static uint32_t last_pkt_ms = 0;

static uint32_t land_start_ms = 0;

static float flip_acc = 0;
static uint32_t flip_start_ms = 0;

#define FAILSAFE_MS 500

#ifdef DATA_LOGGING
static uint32_t log_tick=0;
if(++log_tick%2==0){
    char buf[96];
    int n=snprintf(buf,sizeof(buf),"%.3f,%.3f,%.3f,%.3f,%.4f,%.1f,%.1f\r\n",
        att.roll, att.pitch,
        imu->gx-off->gx, imu->gy-off->gy,
        (float)pkt->throttle/1000.0f,
        roll_out, pitch_out);
    HAL_UART_Transmit(&huart2,(uint8_t*)buf,n,5);
}
#endif

void FC_Init(void){
    PID_Init(&pid_rr, RP_KP,  RP_KI,  RP_KD,  200,500);
    PID_Init(&pid_pr, RP_KP,  RP_KI,  RP_KD,  200,500);
    PID_Init(&pid_yr, YR_KP,  YR_KI,  0,      200,500);
    PID_Init(&pid_ra, ANG_KP, 0,0,    1000,200);
    PID_Init(&pid_pa, ANG_KP, 0,0,    1000,200);
    memset(&att,0,sizeof(att));
    state=FC_DISARMED;
}


static void fly(const RC_Packet *pkt, const ICM_Data *imu,
                const ICM_Offsets *off, uint16_t thr, float dt){
    float rsp = (float)pkt->roll  *30.0f/500.0f;
    float psp = (float)pkt->pitch *30.0f/500.0f;
    float ysp = (float)pkt->yaw   *200.0f/500.0f;
    float rr_sp = PID_Compute(&pid_ra, rsp, att.roll,  dt);
    float pr_sp = PID_Compute(&pid_pa, psp, att.pitch, dt);
    float gx=imu->gx-off->gx, gy=imu->gy-off->gy, gz=imu->gz-off->gz;
    float ro = PID_Compute(&pid_rr, rr_sp, gx, dt);
    float po = PID_Compute(&pid_pr, pr_sp, gy, dt);
    float yo = PID_Compute(&pid_yr, ysp,   gz, dt);
    Motor_Mix(thr,(int16_t)ro,(int16_t)po,(int16_t)yo);
}



void FC_Update(const RC_Packet *pkt, const ICM_Data *imu,
               const ICM_Offsets *off){
    static uint32_t last_us = 0;
    uint32_t now_us = SF_Micros();
    float dt = (last_us==0) ? 0.001f : (float)(now_us-last_us)*1e-6f;
    last_us = now_us;

    SF_Update(imu, off, &att);

    uint32_t now_ms = HAL_GetTick();
    if(pkt) last_pkt_ms = now_ms;


    if((now_ms-last_pkt_ms)>FAILSAFE_MS && state!=FC_DISARMED){
        Motor_Disarm(); state=FC_DISARMED; return;
    }
    if(!pkt) return;

    switch(state){

    case FC_DISARMED:
        if((pkt->flags&0x01) && pkt->throttle<50){
            Motor_Arm();
            PID_Reset(&pid_rr); PID_Reset(&pid_pr); PID_Reset(&pid_yr);
            PID_Reset(&pid_ra); PID_Reset(&pid_pa);
            state=FC_ARMED;
        }
        break;

    case FC_ARMED:
        if(!(pkt->flags&0x01)){ Motor_Disarm(); state=FC_DISARMED; break; }
        if(pkt->throttle>100) state=FC_FLYING;
        Motor_SetAll(0,0,0,0);
        break;

    case FC_FLYING:
        if(!(pkt->flags&0x01)){ Motor_Disarm(); state=FC_DISARMED; break; }
        if(pkt->flags&0x04){ land_start_ms=now_ms; state=FC_AUTO_LAND; break; }
        if((pkt->flags&0x02) && pkt->throttle>300){
            flip_acc=0; flip_start_ms=now_ms; state=FC_FLIP; break;
        }
        fly(pkt,imu,off,pkt->throttle,dt);
        break;

    case FC_AUTO_LAND:{
        uint32_t el  = now_ms - land_start_ms;
        float prog   = (float)el/2500.0f;
        if(prog>1.0f) prog=1.0f;
        uint16_t thr = (uint16_t)((1.0f-prog)*400.0f);
        float az     = imu->az - off->az;
        if((fabsf(az)<0.4f && prog>0.5f) || prog>=1.0f){
            Motor_Disarm(); state=FC_DISARMED; break;
        }

        float gx=imu->gx-off->gx, gy=imu->gy-off->gy;
        float rr_sp=PID_Compute(&pid_ra,0,att.roll,dt);
        float pr_sp=PID_Compute(&pid_pa,0,att.pitch,dt);
        float ro=PID_Compute(&pid_rr,rr_sp,gx,dt);
        float po=PID_Compute(&pid_pr,pr_sp,gy,dt);
        Motor_Mix(thr,(int16_t)ro,(int16_t)po,0);
        break;
    }

    case FC_FLIP:{
        uint32_t el = now_ms - flip_start_ms;
        float gx    = imu->gx - off->gx;
        flip_acc   += fabsf(gx)*dt;
        if(flip_acc>=360.0f || el>800){
            PID_Reset(&pid_rr); state=FC_FLYING; break;
        }
        Motor_Mix(800,500,0,0);
        break;
    }
    }
}

FC_State FC_GetState(void){ return state; }

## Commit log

2026-04-16 Initial commit
    PCBs, STEP files, Firmware and ML Pipeline files added
    [Drone Case.step, Drone FC.kicad_pcb, Drone FC.kicad_sch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]
2026-04-16 added BOM
2026-04-16 updated BOM
2026-04-16 cleaned up drone FC PCB
2026-04-16 cleaned up drone RC PCB
2026-04-18 added BOM to readme (as requested in the docs)
2026-04-18 Turned BOM into CSV (as requested in docs)
    [BOM.csv]
2026-04-21 Update README with PCB update note
    Updated README to reflect recent changes to PCBs after fixing KiCad issues.
2026-04-21 added fixed PCBs
    [Drone FC.kicad_pcb, Drone RC.kicad_pcb]

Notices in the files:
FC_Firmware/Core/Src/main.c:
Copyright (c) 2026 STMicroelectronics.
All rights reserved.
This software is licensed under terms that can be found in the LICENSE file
